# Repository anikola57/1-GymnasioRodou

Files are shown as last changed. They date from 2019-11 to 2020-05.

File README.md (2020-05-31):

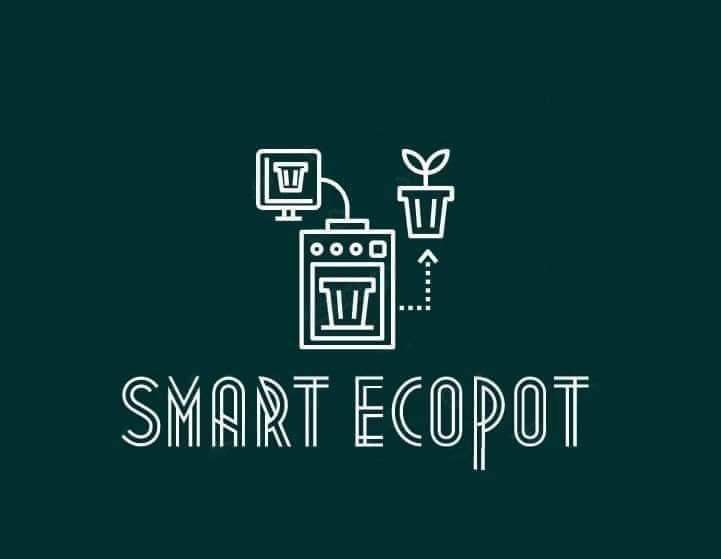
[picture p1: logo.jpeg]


---
# Smart ecoPOT
 Έξυπνο σύστημα διαχείρισης ποτίσματος

- [Περιγραφή](#Περιγραφή)
- [Θεματική](#Θεματική)
- [Τεχνολογίες - υλοποίηση](#Τεχνολογίες-υλοποίηση)
- [Ομάδα έργου](#Ομάδα)
- [Οργάνωση του έργου](#Οργάνωση)
- [Προϋπολογισμός](#Προϋπολογισμός)
- [Σύνδεσμοι](#Σύνδεσμοι)

>## Περιγραφή
Το `Smart ecoPOT` είναι μία «έξυπνη» γλάστρα στην οποία το φυτό ποτίζεται αυτόματα σύμφωνα με τις ανάγκες του. Η συγκεκριμένη λύση βασίζεται σε μετρήσεις της υγρασίας του χώματος στη γλάστρα και όταν αυτή μειωθεί κάτω από ένα όριο ενεργοποιείται μία αντλία νερού και το φυτό ποτίζεται με την απαιτούμενη ποσότητα νερού.

Το προτεινόμενο σχέδιο γλάστρας αποτελείται από τρία μικρά γλαστράκια εξάγωνου σχήματος και διαφορετικών υψών στα οποία μπορούν να φυτευτούν διάφορα φυτά. Στην κατασκευή περιλαμβάνεται η δεξαμενή νερού και ένας χώρος στον οποίο μπαίνει το ηλεκτρονικό κύκλωμα για τον έλεγχο του ποτίσματος.

Με τον έλεγχο της υγρασίας του χώματος και της παροχής νερού, τα φυτά μπορούν να αναπτυχθούν πιο υγιή. Τόσο η έλλειψη νερού όσο και το υπερβολικό πότισμα μπορούν να προκαλέσουν την καταστροφή του φυτού, ιδιαίτερα όταν πρόκειται για ευαίσθητα στην πρόσληψη νερού μυρωδικά. Με το προτεινόμενο σχέδιο το φυτό προσλαμβάνει την ποσότητα νερού που χρειάζεται για την καλύτερη ανάπτυξή του ακριβώς όταν τη χρειάζεται.

Επιπλέον, δεν απαιτείται από τον ιδιοκτήτη του φυτού να θυμάται κάθε πότε πρέπει να το ποτίσει. Το φυτό είναι αυτόνομο και απαιτείται μόνο η πλήρωση της δεξαμενής με νερό όποτε χρειάζεται. Στην περίπτωση που το νερό στη δεξαμενή εξαντλείται θα ανάβει ένα κόκκινο φωτάκι έτσι ώστε να ενημερώνεται ο ιδιοκτήτης ότι πρέπει να τη γεμίσει. Ιδιαίτερα στα απαιτητικά αστικά περιβάλλοντα αυτό είναι μία ελάφρυνση από ένα καθημερινό καθήκον.

Ένα βασικό πλεονέκτημα της κατασκευής είναι ότι γίνεται εξοικονόμηση νερού. Χρησιμοποιείται μόνο όσο νερό χρειάζεται και στο χρόνο που χρειάζεται. Αυτό είναι ιδιαίτερα σημαντικό στην εφαρμογή σε μεγαλύτερη κλίμακα.

Η γλάστρα μπορεί εύκολα να εκτυπωθεί σε 3D εκτυπωτή με βάση το σχέδιο, σε διάφορα χρώματα και μεγέθη. Είναι σχεδιασμένη έτσι ώστε να συναρμολογείται εύκολα και να χωρίζεται σε κομμάτια για να γεμίσει η δεξαμενή νερού, να πλυθεί, να ανανεωθούν τα φυτά ή ακόμα να αλλαχτούν τα εξαρτήματα της κατασκευής.

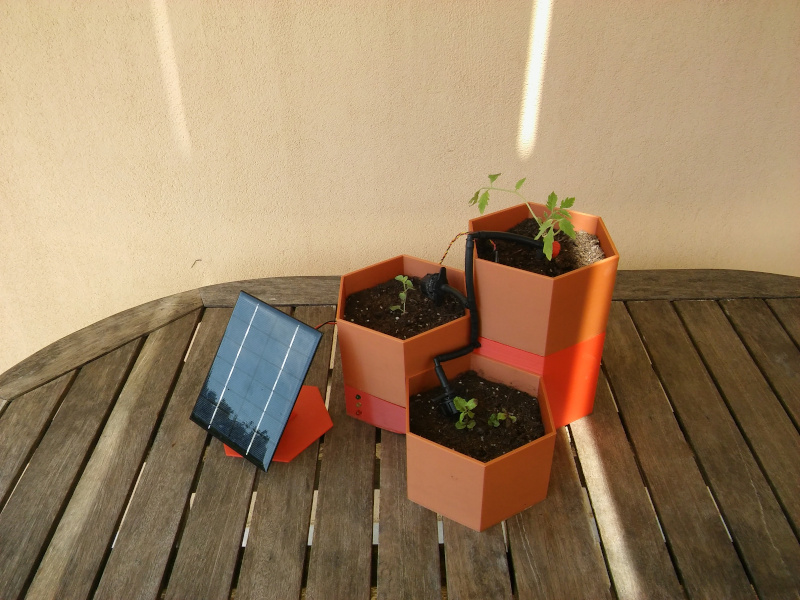
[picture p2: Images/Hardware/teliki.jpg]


Δείτε το βίντεο με την περιγραφή της κατασκευής μας.

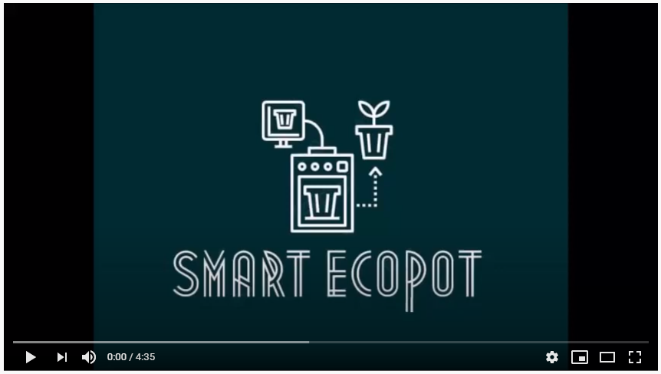
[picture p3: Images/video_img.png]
Βίντεο (https://www.youtube.com/watch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)


Και μία  [παρουσίαση](./Docs/GLASTRA.pdf) που κάναμε διαδικτυακά.

>## Θεματική
Το συγκεκριμένο έργο εντάσσεται στη θεματική της αστικής κηπουρικής, η οποία αναφέρεται στην ανάπτυξη φυτών στις πόλεις και γύρω από αυτές. Η αστική κηπουρική αποτελεί μέρος του αστικού οικοσυστήματος και της οικονομίας των πόλεων. 

Η αστική κηπουρική συμβάλει στη βελτίωση της ποιότητας της τροφής που καταναλώνεται στα αστικά κέντρα και στην προώθηση πιο υγιεινής διατροφής. Συγχρόνως, μειώνει το κόστος ενός νοικοκυριού για διατροφή αλλά και το οικολογικό αποτύπωμα της καλλιέργειας (γη, νερό, καύσιμα από τη μεταφορά της τροφής).

Η συγκεκριμένη πρόταση θα μπορούσε να επεκταθεί και για τη διαχείριση μεγαλύτερων αγροτικών εκτάσεων. Η διαχείριση του ποτίσματος μίας καλλιέργειας με αυτόν τον τρόπο θα επέφερε μεγαλύτερη εξοικονόμηση νερού και υγιείς καλλιέργειες.

>## Τεχνολογίες-υλοποίηση
Αφορμή και κίνητρο για τη συμμετοχή μας στο διαγωνισμό, είναι η αξιοποίηση του αναβαθμισμένου εξοπλισμού που παρέλαβε το σχολείο μας την περσινή χρονιά. Σε αυτόν περιλαμβάνεται ένας 3D εκτυπωτής, ένα 3D scanner, 8 εκπαιδευτικά set `Arduino Uno` και 10 σταθμοί εργασίας με `Raspberry pi`.  
Για την απόκτηση τεχνογνωσίας σχετικά με τον εξοπλισμό αυτό αξιοποιήθηκαν αποκλειστικά πηγές από το διαδίκτυο και εθελοντές ειδικοί σε σχετικούς τομείς.

Για την εκτύπωση της γλάστρας χρησιμοποιήθηκε ο 3D εκτυπωτής του Εργαστηρίου Τεχνολογίας του σχολείου. Με την αξιοποίηση του 3D εκτυπωτή κατασκευάζεται μία ολοκληρωμένη διάταξη, με τη γλάστρα, τη δεξαμενή νερού και τα ηλεκτρονικά, προσαρμοσμένη στις απαιτήσεις του έργου. 

Το αρχικό σχέδιο της γλάστρας έγινε στο online ελεύθερο λογισμικό `Tinkercad`. Στη συνέχεια λόγω μεγαλύτερης ευελιξίας προτιμήθηκε το επίσης ελεύθερο λογισμικό `Blender`. 
Αρχικό σχέδιο κατασκευής στο `Tinkercad` 

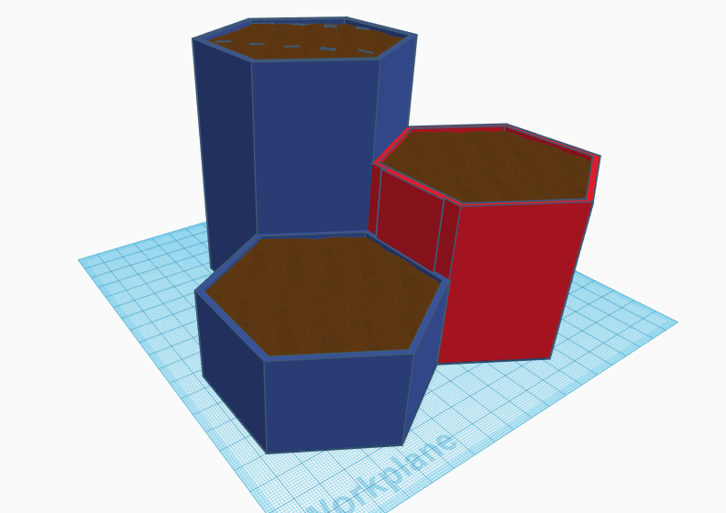
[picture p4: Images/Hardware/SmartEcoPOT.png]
 

Τελικό σχέδιο κατασκευής στο `Blender` 

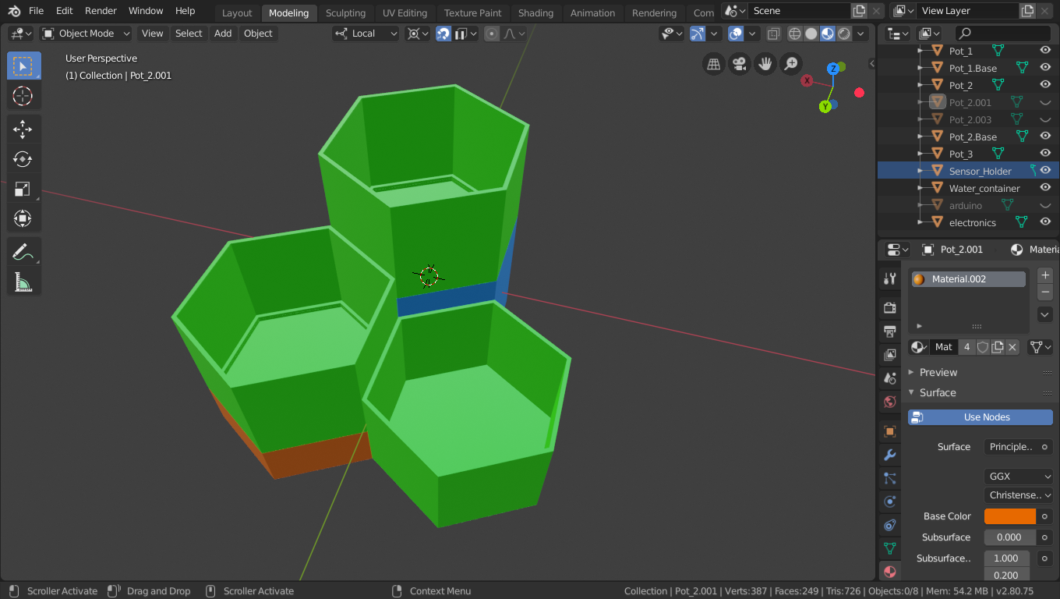
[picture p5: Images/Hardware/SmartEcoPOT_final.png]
 

Η κατασκευή αποτελείται από τρία κανονικά εξαγωνικά πρίσματα διαφορετικού ύψους, στο πάνω μέρος των οποίων έχουν προσαρτηθεί γλαστράκια ίδιου σχήματος και ύψους με το μικρότερο από τα πρίσματα. Τα γλαστράκια είναι αποσπώμενα έτσι ώστε να μπορούν να γεμίσουν με χώμα και να φυτευτούν. Το κάτω μέρος από το μεγαλύτερο από τα εξάγωνα είναι η δεξαμενή νερού και στο αντίστοιχο κάτω μέρος από το μεσαίο γλαστράκι μπαίνει το κύκλωμα με το Arduino. 

Για τον έλεγχο της στάθμης του νερού και της υγρασίας του χώματος χρησιμοποιείται `Arduino Uno`. Για τη μέτρηση της υγρασίας του χώματος χρησιμοποιείται αναλογικός αισθητήρας υγρασίας ο οποίος δίνει μία τιμή στο πρόγραμμα ανάλογα με την υγρασία του χώματος. Το πρόγραμμα μετατρέπει αυτή την τιμή σε ποσοστό %. Για τη μέτρηση της στάθμης νερού τοποθετηθηκε στη δεξαμενή ένας δεύτερος αισθητήρας υγρασίας που δίνει σήμα ανάλογα με τη στάθμη του νερού. Υπάρχει ακόμα μία αντλία ποτίσματος, η οποία συνδέεται μέσω κατάλληλης διάταξης για την ενίσχυση του ρεύματος, σε μία ψηφιακή έξοδο του Arduino. Το οριστικό σχηματικό διάγραμμα του κυκλώματος έγινε στο fritzing και είναι το παρακάτω:

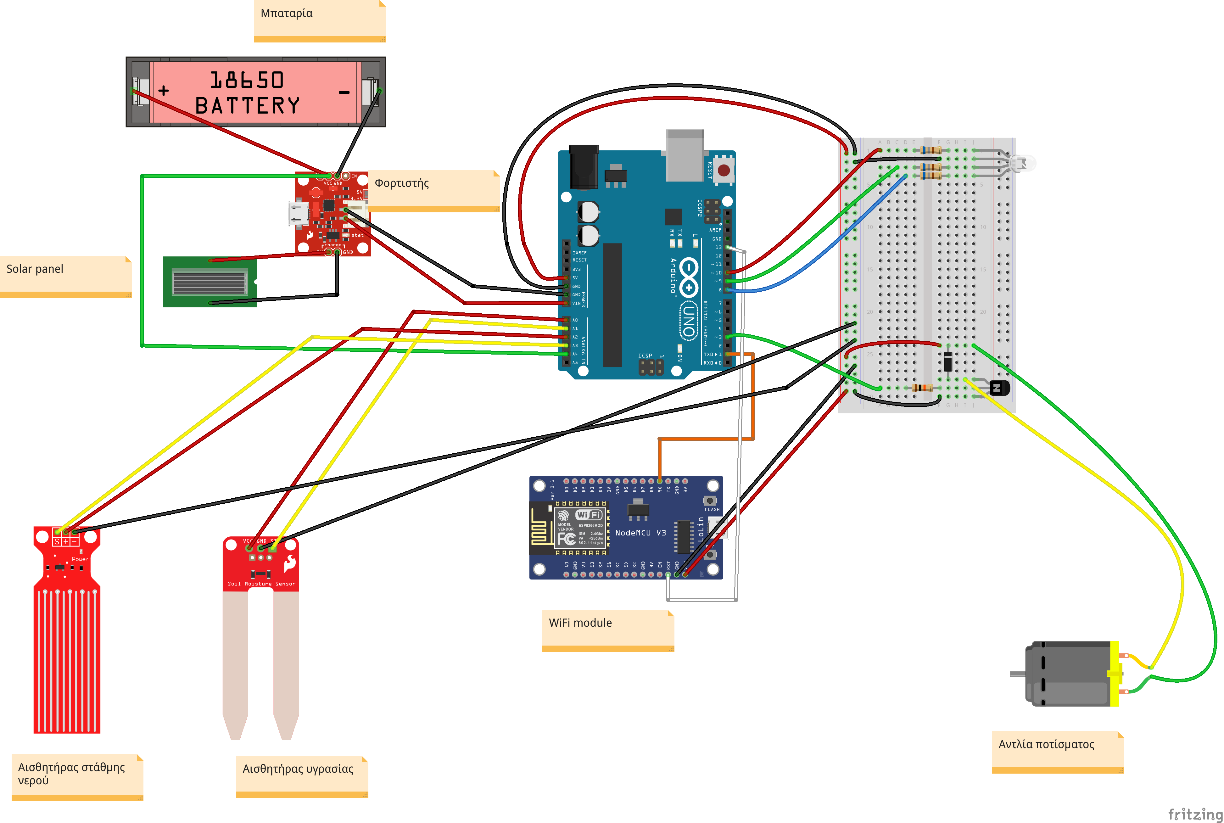
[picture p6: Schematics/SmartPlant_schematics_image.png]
 

Για την προβολή της κατάστασης του συστήματος υπάρχουν ενδεικτικά led τα οποία ειδοποιούν για την κατάσταση της υγρασίας του χώματος, την επάρκεια νερού στη δεξαμενή και την κατάσταση ποτίσματος. Το κύκλωμα τροφοδοτείται είτε από τροφοδοτικό είτε εναλλακτικά από επαναφορτιζόμενη μπαταρία με φωτοβολταϊκό πάνελ. Για τη στήριξη του φωτοβολταϊκού σχεδιάστηκε και τυπώθηκε στον 3D εκτυπωτή μία βάση.

Το λογισμικό για τον έλεγχο των αισθητήρων, της αντλίας και των ενδείξεων αναπτύχθηκε στην πλατφόρμα Arduino. Ένα βασικό διάγραμμα ροής του προγράμματος υπάρχει στον φάκελο [Docs](./Docs/flowchart_1.pdf)

Για την αναπαραγωγή του έργου δίνεται το σχέδιο της [γλάστρας](./3D/) για εκτύπωση σε 3D εκτυπωτή, το σχέδιο του [κυκλώματος](./Schematics/) και το [πρόγραμμα](./Source/)  .

Στην κατασκευή ενσωματώθηκε ένα WiFi module για τη βελτίωση της εποπτείας της κατάστασης. Μέσω αυτού στέλνονται τα δεδομένα της γλάστρας, όπως υγρασία χώματος και στάθμη νερού, στην πλατφόρμα ThingSpeak. Από εκεί υπάρχει η δυνατότητα παρακολούθησης της κατάστασης σε πραγματικό χρόνο μέσω μίας ιστοσελίδας.

>## Ομάδα
Στο έργο συμμετείχαν μαθητές της Β' τάξης του 1ου Γυμνασίου Ρόδου υπό την καθοδήγηση της καθηγήτριας τεχνολογίας Αγγελικής Νικολάου.
Οι συναντήσεις των μαθητών γινόντουσαν μετά το σχολικό ωράριο στο χώρο του σχολείου. Μετά το κλείσιμο των σχολείων λόγω κοροναϊού, οι συναντήσεις συνεχίστηκαν με το https://jitsi.org/jitsi-meet/.  Αν και όλοι οι μαθητές συνεργάστηκαν μεταξύ τους για το έργο, δημιουργήθηκαν κάποιες ομάδες οι οποίες ανέλαβαν ένα μέρος του. Συγκεκριμένα οι ομάδες είναι οι ακόλουθες:

    Προγραμματιστές
    Ασχολήθηκαν κυρίως με την ανάπτυξη του λογισμικού για το Arduino.
---
    Σχεδιαστές
    Σχεδίασαν τη γλάστρα για την εκτύπωση στον 3D εκτυπωτή. 
---
    Ηλεκτρονικοί
    Σχεδίασαν το κύκλωμα και συντόνισαν την υλοποίηση της κατασκευής.  

Φωτογραφίες της ομάδας επί το έργον, υπάρχουν στον φάκελο [Images/Act](./Images/Act).

> ## Οργάνωση
Ο τρόπος οργάνωσης και υλοποίησης καθώς και το πλαίσιο του έργου περιγράφεται αναλυτικά στο σχετικό [αρχείο](./Docs/ConceptOfProject.pdf).

> ## Προϋπολογισμός
Κόστος έργου για τη βασική κατασκευή:

Ειδος|Τιμή
---|---:
Arduino Nano OEM|4,50€
Βυθιζόμενη αντλία|5€
Σωληνάκι|0,60€
Transistor|0,05€
Αντιστάσεις|0,05€
Καλώδια|1€
LED|0,20€
Αισθητήρας στάθμης νερού|2€
Αισθητήρες υγρασίας εδάφους|2€
Breadboard|1€
PLA|6€
ΣΥΝΟΛΟ|22,40€

Κόστος έργου με επιλογή για τροφοδοτικό:

Ειδος|Τιμή
---|---:
Βασική κατασκευή|22,40€
Τροφοδοτικό|5€
ΣΥΝΟΛΟ|27,40€

Κόστος έργου με επιλογή για φωτοβολταϊκό και επαναφορτιζόμενη μπαταρία:

Ειδος|Τιμή
---|---:
Βασική κατασκευή|22,40€
Φωτοβολταϊκό πάνελ 5v, 1w|3€
Επαναφορτιζόμενη μπαταρία 18650 3400mAh|4,40€
Κύκλωμα φόρτισης φωτοβολταϊκού CN3065|3,80€
Κύκλωμα φόρτισης μπαταρίας 134N3P|1,20€
ΣΥΝΟΛΟ|34,80€

Το κόστος για την επέκταση της κατασκευής με το wifi module:

Ειδος|Τιμή
---|---:
NodeMCU|7€

> ## Σύνδεσμοι

2ος Πανελλήνιος Διαγωνισμός Ανοιχτών Τεχνολογιών στην Εκπαίδευση https://robotics.ellak.gr/

Arduino https://www.arduino.cc

3D printer Ultimaker 2+ https://ultimaker.com/3d-printers/ultimaker-2-plus 

Tinkercad https://www.tinkercad.com/

fritzing https://fritzing.org/

ThingSpeak https://thingspeak.com/

Blender https://www.blender.org/

Αστική κηπουρική https://www.ruaf.org/urban-agriculture-what-and-why

1ο Γυμνάσιο Ρόδου http://1gym-rodou.dod.sch.gr/wp/

---

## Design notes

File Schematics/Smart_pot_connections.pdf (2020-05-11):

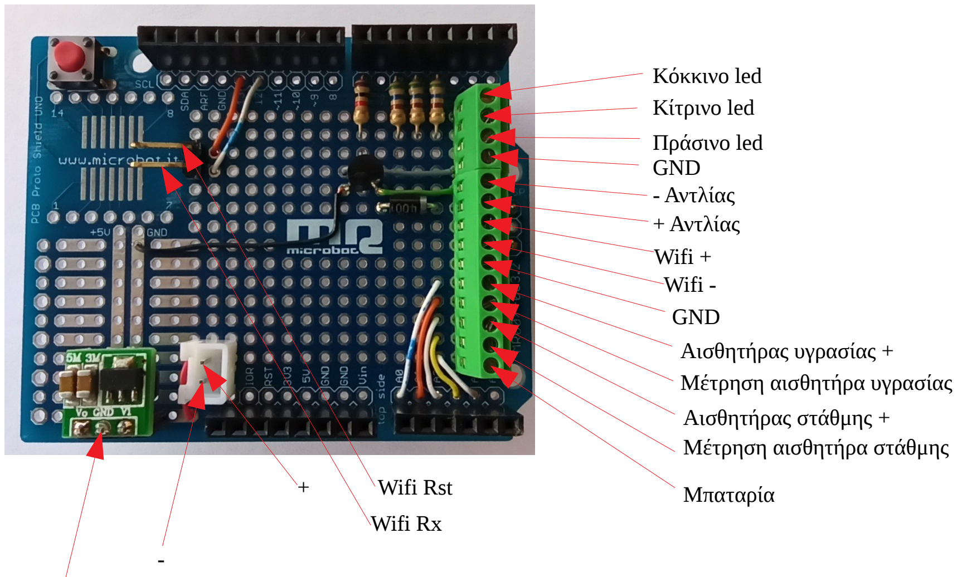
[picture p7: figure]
Κόκκινο ledled Κίτρινο ledled Πράσινο ledled GND - ledΑντλίας + ledΑντλίας Wifi led+ Wifi led- GND Αισθητήρας ledυγρασίας led+ Μέτρηση ledαισθητήρα ledυγρασίας Αισθητήρας ledστάθμης led+ Μέτρηση ledαισθητήρα ledστάθμης; Μπαταρία +; Wifi ledRx; Wifi ledRst

Μετατροπέας led4.2v σε 5vv ledσε led5vv

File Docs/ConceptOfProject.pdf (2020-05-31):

# SMART ECOPOT

1

# Ο ΓΥΜΝΑΣΙΟ ΡΟΔΟΥ

### Υπεύθυνη εκπαιδευτικός: Αγγελική Νικολάου, Αρχιτέκτων

# ΤΟ CONCEPT ΤΟΥ ΕΡΓΟΥ ΜΑΣ

Το Μάρτιο του 2019 το σχολείο παρέλαβε αναβαθμισμένο τεχνολογικό εξοπλισμό για τον οποίο δεν υπήρχε πρόβλεψη που θα τοποθετηθεί και από ποιους εκπαιδευτικούς θα αξιοποιηθεί. Επιπλέον επειδή δεν υπήρξε καμία επιμόρφωση, το υλικό αυτό παρέμενε αχρησιμοποίητο.

Με αφορμή την επιθυμία ομάδας παιδιών της Β΄ Γυμνασίου να χρησιμοποιήσουμε τον τρισδιάστατο εκτυπωτή, αναλάβαμε τη δημιουργία ενός έργου, πέρα από τα πλαίσια κάποιου μαθήματος. Ενός πρότζεκτ που θα εντασσόταν σε ένα πλαίσιο συνεργασιών και θα είχε σκοπό που θα υπερέβαινε όλους μαζί και τον καθένα ξεχωριστά, μαθητές και εκπαιδευτικό.

Θεωρούμε ότι η εμπειρία αυτού του τύπου έργων για την εποχή μας, την εποχή των ραγδαίων αλλαγών, είναι πολύ σημαντική για ένα παιδί Γυμνασίου, το οποίο έχει την αναπτυξιακή ωριμότητα να καταλάβει τη διαδικασία, να τη διεκπεραιώσει και να τη δέσει με την εργασία των άλλων-συνεργατών.

Όσον αφορά τη θέση μας στον παιδαγωγικό χάρτη, γνωρίζουμε ότι η επιστήμη τείνει προς την κατεύθυνση της ανάλυσης αλλά και ότι στη σύγχρονη πραγματικότητα η γνώση είναι σωρευτική. Στην τεχνολογία γενικότερα κάνουμε πράγματα, κινούμενοι προς την κατεύθυνση του σχεδιασμού και της κατασκευής. Στόχος μας είναι τα παιδιά να συνεργαστούν και να αξιοποιήσουν τη γνώση των άλλων, προσπαθώντας να λύσουν ένα πρόβλημα. Εν προκειμένω η ανάλυση καταλαμβάνει μικρότερο μέρος και μεγαλύτερη έμφαση δίνεται στο σχεδιασμό της λύσης του προβλήματος και τη σύνθεση.

Ανατρέχοντας στο διαδίκτυο είναι γνωστό ότι μπορούμε να εντοπίσουμε, να αξιοποιήσουμε και να ωφεληθούμε από τη γνώση άλλων, οι οποίοι πριν από εμάς «ανακάλυψαν τον τροχό». Δεν αγνοούμε αυτού του τύπου τη γνώση, αλλά αντιθέτως προσπαθούμε να την αξιοποιήσουμε προς όφελος όλων. Το παιδί παρακολουθώντας αυτή τη διαδικασία και συμμετέχοντας στην αναζήτηση, αποκτά μια πολύ σημαντική και ωφέλιμη εμπειρία: ότι αξιοποιώντας τη γνώση των άλλων για να λύσουμε ένα πραγματικό πρόβλημα, ίσως οδηγηθούμε προς την καινοτομία. Με αυτό τον τρόπο, μπορούμε να του θέσουμε ερωτήματα, που θα του δημιουργήσουν την επιθυμία να ανελιχθεί σε πιο σύνθετα ερωτήματα και που ίσως το οδηγήσουν σε νέα γνώση αργότερα.

Η παρουσίαση μας αυτή, μεταξύ άλλων έχει σκοπό να καταθέσει την εμπειρία που αποκτήθηκε από τη σκοπιά που περιγράψαμε παραπάνω, ώστε στο μέλλον να υπάρξουν περισσότεροι εκπαιδευτικοί, από διαφορετικές ειδικότητες που θα εμπλακούν, με στόχο τη δημιουργική επίλυση προβλημάτων και την αξιοποίηση πόρων της παγκόσμιας κοινότητας που διακινεί και διαμοιράζεται ανοιχτό υλικό.

# ΟΡΓΑΝΩΣΗ ΤΟΥ PROJECT

### Σεπτέμβριος 2019

Έναρξη του πρότζεκτ, με την ανακοίνωση του διαγωνισμού ο οποίος αποτέλεσε μια καλή ευκαιρία εμπλοκής μαθητών στην αξιοποίηση του αναβαθμισμένου ψηφιακού εξοπλισμού που διέθετε το 1ο Γυμνάσιο Ρόδου, τον Μάρτιο του 2019.

Η ομάδα συγκροτήθηκε άμεσα (12 μαθητές Α΄ και Β΄ Γυμνασίου) και οι συναντήσεις ορίστηκαν κάθε Τρίτη μια ώρα, μετά το σχόλασμα και τις Κυριακές για περισσότερο χρόνο. Με ιδεοθύελλα και αναζήτηση στο ίντερνετ αλλά και από το περιβάλλον των γνωστών των παιδιών, καταλήξαμε στον τομέα της αστικής κηπουρικής και της γεωργίας ακριβείας. Αποφασίσαμε να δημιουργήσουμε ένα αυτόνομο σύστημα από γλάστρες, οι οποίες θα λύνουν το πρόβλημα της καλλιέργειας σε αστικό προβάλλον, (βεράντα, ταράτσα, κήπο, αγρόκτημα). Με δυνατότητα ποτίσματος όταν το έχει ανάγκη το φυτό και αισθητήρες για να ειδοποιούν τον κάτοχο για τα στοιχεία που τον ενδιαφέρουν, όπως, υγρασία εδάφους, στάθμη νερού και άλλα χαρακτηριστικά.

Επειδή το πρότζεκτ ξεπερνούσε τις δυνατότητες όλων μας, παιδιών και εκπαιδευτικού, και επειδή η γνώση υπάρχει «εκεί έξω», δύο ήταν οι επόμενες κινήσεις. Πρώτον, να δούμε τι έχουν κάνει άλλοι πριν από εμάς και δεύτερον ποιους θα εμπλέξουμε εθελοντικά κυρίως στο κομμάτι του κώδικα και των ηλεκτρονικών.

Βήμα 1

ο

Αναζήτηση στο διαδίκτυο για πρότζεκτ που έχουν υλοποιηθεί με arduino.

https://www.instructables.com/circuits/arduino/projects/

https://www.instructables.com/circuits/projects/

https://www.instructables.com/id/9-12-Projects-High-School/

https://create.arduino.cc/projecthub/projects/tags/kids

https://www.makerspaces.com/15-simple-arduino-uno-breadboard-projects/

https://www.circuito.io/blog/arduino-projects-for-beginners/

https://www.youtube.com/watch?v=PfvqunpN7M4

Εκπαιδευτικό Υλικό για Arduino Uno

Προγραμματίζοντας με τον μικροελεγκτή Arduino

http://users.sch.gr/manpoul/docs/arduino/ProgrammingArduino.pdf

http://3gym-igoum.thesp.sch.gr/images/Arduino/book.pdf

https://www.vodafonegenerationnext.gr/learn/arduino-basics

http://robotics-edu.gr/data/arduino/arduino_paliouras.pdfhttps://www.youtube.com/watch?v=62MGqPIyoDg

https://www.youtube.com/watch?v=SlU7ADUIgtI

Βήμα 2

ο
: Αναζήτηση συνεργατών με γνώσεις χρήσης Arduino και ηλεκτρονικών

Αξιοποιώντας το προσωπικό μαθησιακό δίκτυο (PLN), έγιναν οι παρακάτω δράσεις:

- Στην πρώτη συγκέντρωση ενημέρωσης γονέων μετά τον αγιασμό του σχολείου, ανακοινώθηκε η πρόσκληση εθελοντικής συμμετοχής γονέων-συνεργατών για την αξιοποίηση του ψηφιακού εξοπλισμού του σχολείου.
- Στάλθηκαν emails με πρόσκληση προς όλους τους εκπαιδευτικούς της Ρόδου, από τις διευθύνσεις Πρωτοβάθμιας και Δευτεροβάθμιας Εκπαίδευσης Δωδεκανήσου, για εθελοντική συμμετοχή σε καινοτόμο πρόγραμμα.
- Στάλθηκαν emails από τη γραμματεία της Σχολής Ανθρωπιστικών σπουδών του Παν/μίου Αιγαίου προς όλους, διδακτικό προσωπικό και φοιτητές.
- ‘Έγινε αναζήτηση εθελοντών μέσω του Tipping point https://www.thetippingpoint.org.gr/ και 100 mentors https://platform.100mentors.com/community/tippingpoint

Το αποτέλεσμα ήταν να βρεθούν εθελοντές: οι γονείς μαθητή μας, οι κ. & κ. Γρίβας (μαθηματικός και ηλεκτρονικός), ο διδάσκων από το Παν/μιο Αιγαίου κ. Ν. Ταψής (φυσικός) και ο μέντορας από το tipping point κ. Η. Ψυρούκης (ηλεκτρολόγος μηχ/κος).

### Οκτώβριος- Νοέμβριος- Δεκέμβριος 2019

Διατύπωση του προβλήματος και η λύση

Διατυπώθηκε το πρόβλημα που αντιμετωπίζουν οι πολυάσχολοι κάτοικοι της πόλης, όταν καλλιεργούν φυτά σε βεράντες, ταράτσες ή κήπους.

Πρόβλημα: Έλλειψη νερού στο φυτό ή σπατάλη νερού, όταν χρησιμοποιούνται τα γνωστά συστήματα αυτόματου ποτίσματος, που κυκλοφορούν στην αγορά.

Λύση: Σωστή ποσότητα νερού που χρειάζεται το φυτό, την ώρα που το χρειάζεται με προγραμματισμό ποτίσματος, από αισθητήρα υγρασίας χώματος. Η αντλία νερού που θα βυθίζεται σε δεξαμενή ενσωματωμένη στη γλάστρα, θα περιέχει αισθητήρα στάθμης νερού για να δίνει φωτεινό σήμα (θα ανάβει led) όταν το νερό κατεβαίνει κάτω από ένα επίπεδο. Η επαναφορτιζόμενη πηγή θα φορτίζεται από ηλιακό πάνελ.

Εξοπλισμός και αναζήτηση στο διαδίκτυο υλικών-ηλεκτρονικών κατασκευής

Γλάστρα, αισθητήρας υγρασίας χώματος, δεξαμενή νερού, αισθητήρας στάθμης νερού, αντλία νερού, σωληνάκια ποτίσματος, λεντάκια με ενδείξεις για τη στάθμη του νερού στη δεξαμενή, μικροελεγκτής Arduino Uno, ηλιακό πάνελ για τη φόρτιση της μπαταρίας και ασύρματη επικοινωνία των δεδομένων των αισθητήρων.

Διάγραμμα ροής

Τα παιδιά δημιούργησαν στον πίνακα του σχολείου το διάγραμμα ροής.

Εξοικείωση με τον προγραμματισμό

Η ομάδα μέσω της πλατφόρμας του The tipping point, άρχισε μαθήματα εξοικείωσης με τον προγραμματισμό για Arduino. Οι μαθητές ανταποκρίθηκαν με ενθουσιασμό στην από απόσταση
διδασκαλία. | Από | το | διαδικτυακό | υλικό
http://users.sch.gr/manpoul/docs/arduino/ProgrammingArduino.pdf | επιλεκτικά | οι | μαθητές
εξερεύνησαν τις βασικές αρχές στον προγραμματισμό του Arduino και στα κυκλώματα.

Στη συνέχεια με κατάλληλη καθοδήγηση τα παιδιά αναζήτησαν στο διαδίκτυο δημοσιευμένα προγράμματα που αφορούσαν αυτόνομο πότισμα, αισθητήρες υγρασίας, λειτουργία αντλίας και LED.

Επέλεξαν | το | πρόγραμμα | που | ικανοποιούσε | τις | βασικές | αρχές | της | λύσης | τους
https://www.youtube.com/watch?v=T_tpKoNCVYw και χρησιμοποίησαν ως βάση αυτόν τον κώδικα, για να τον επεκτείνουν ώστε να ικανοποιεί τις ανάγκες του δικού τους πρότζεκτ.

Στις επόμενες συναντήσεις χωρίσαμε τον κώδικα σε τμήματα και πειραματιστήκαμε με κομμάτια του κώδικα που αφορούσαν στα παρακάτω:

1. Λειτουργία LED
2. Λειτουργία αισθητήρα υγρασίας χώματος
3. Λειτουργία αντλίας στη δεξαμενή νερού
4. Λειτουργία στάθμης νερού στη δεξαμενή

### Ιανουάριος 2020

ΣΧΕΔΙΑΣΜΟΣ ΤΡΙΣΔΙΑΣΤΑΤΟΥ ΜΟΝΤΕΛΟΥ ΤΗΣ ΓΛΑΣΤΡΑΣ

Αρχικά ο σχεδιασμός της γλάστρας έγινε στο χαρτί. Στη συνέχεια δημιουργήθηκε μακέτα του συστήματος των γλαστρών με μακετόχαρτο, για να δοκιμαστούν τα ηλεκτρονικά και να ελεγχτούν οι διαστάσεις, πριν τη σχεδίαση στον υπολογιστή.

Στη συνέχεια τα παιδιά άρχισαν να σχεδιάζουν τη γλάστρα με το πρόγραμμα Tinkercad, το οποίο είναι online και πολύ φιλικό για τα παιδιά γυμνασίου, αφού πρώτα αναζήτησαν στο διαδίκτυο tutorials. Να σημειωθεί ότι το ίδιο το Tinkercad παρέχει βίντεο με οδηγίες.

Με το Tinkercad έγινε η αρχική σχεδίαση της γλάστρας, αν και κάποια παιδιά είχαν βασικές γνώσεις Sketchup. Τελικά ένα μαθητής έμαθε το σχεδιαστικό πρόγραμμα Blender https://www.blender.org/, στο οποίο έγινε και το τελικό, βελτιωμένο σχέδιο του συστήματος των γλαστρών.

Τα τμήματα του συστήματος εκτυπώθηκαν με PLA, βιοδιασπώμενο υλικό, από τον εκτυπωτή του σχολείου, αφού πρώτα έγιναν οι κατάλληλες παραμετροποιήσεις με το πρόγραμμα CURA. Οι δοκιμές και οι αποτυχίες στην τρισδιάστατη εκτύπωση, ήταν ο τρόπος που οδήγησε στο τελικό αποδεκτό αποτέλεσμα.

### Φεβρουάριος 2020

Ολοκληρώθηκε το πρόγραμμα που δημοσιεύθηκε στο Github https://github.com/anikola57/1-GymnasioRodou (https://github.com/anikola57/1-GymnasioRodou) καθώς κα η εκτύπωση της γλάστρας.

Οι πρώτες δοκιμές των ηλεκτρονικών στην εκτυπωμένη γλάστρα έγιναν στο σχολείο.

### Μάρτιος 2020

Καθώς η ολοκλήρωση του έργου φαινόταν ότι πλησίαζε, η ομάδα σκέφτηκε να κάνει κάποιες βελτιώσεις και επεκτάσεις στο σύστημα των γλαστρών. Επικράτησε η πρόταση το σύστημα να είναι ενεργειακά αυτόνομο και να ελέγχεται από απόσταση.

Σε αυτή τη φάση σταμάτησαν οι δια ζώσης συναντήσεις στο σχολείο λόγω κορονοϊού.

Οι συναντήσεις πλέον γινόντουσαν με το https://jitsi.org/jitsi-meet/. Η γλάστρα μεταφέρθηκε στο σπίτι μαθητή της ομάδας. Με τη βοήθεια του γονέα, προστέθηκε το ηλιακό πάνελ και η ασύρματη επικοινωνία του συστήματος με ιστοσελίδα για τον έλεγχο των δεδομένων από απόσταση (https://thingspeak.com/channels/1026147).

Η οργάνωση της παρουσίασης έγινε και αυτή από απόσταση. Οι μαθητές συνεργάστηκαν και βιντεοσκόπησαν, με αρκετή δυσκολία, τον εαυτό τους για να δημιουργηθεί το τελικό βίντεο της παρουσίασης, το οποίο είναι στο https://www.youtube.com/watch?v=l_-LzqQXOXw.

Φωτογραφίες εν ώρα δράσης

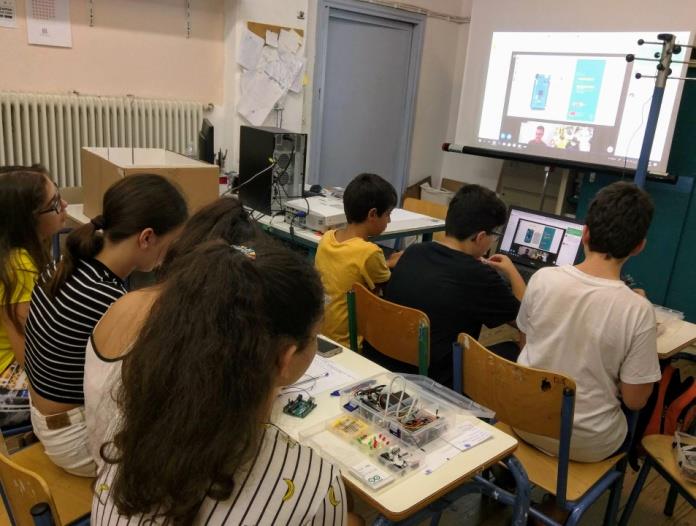
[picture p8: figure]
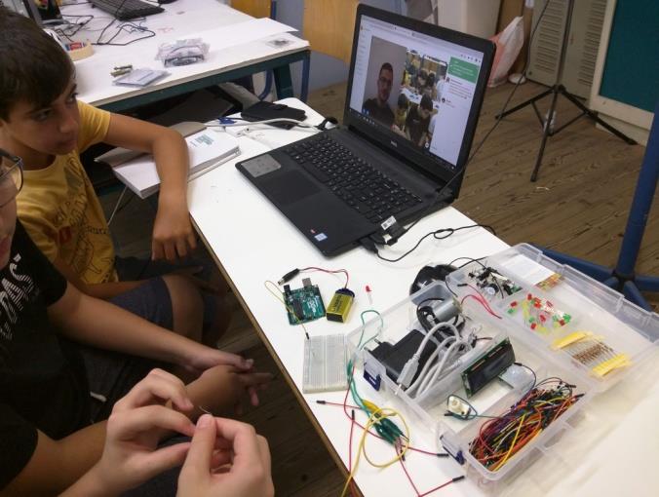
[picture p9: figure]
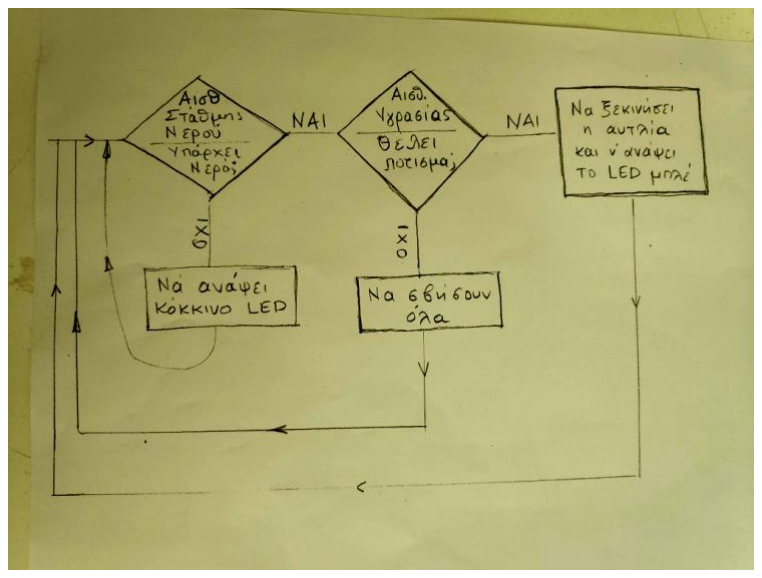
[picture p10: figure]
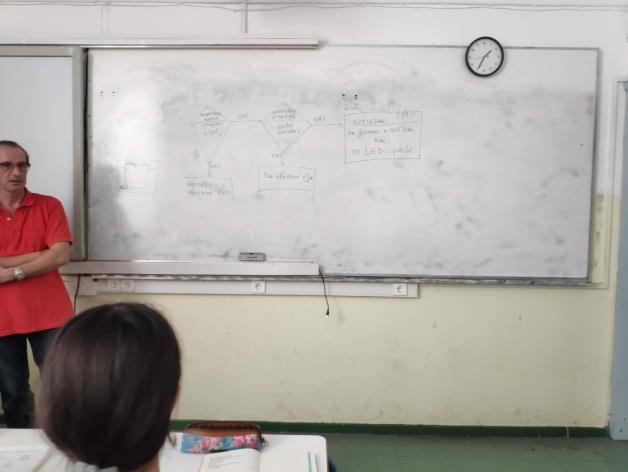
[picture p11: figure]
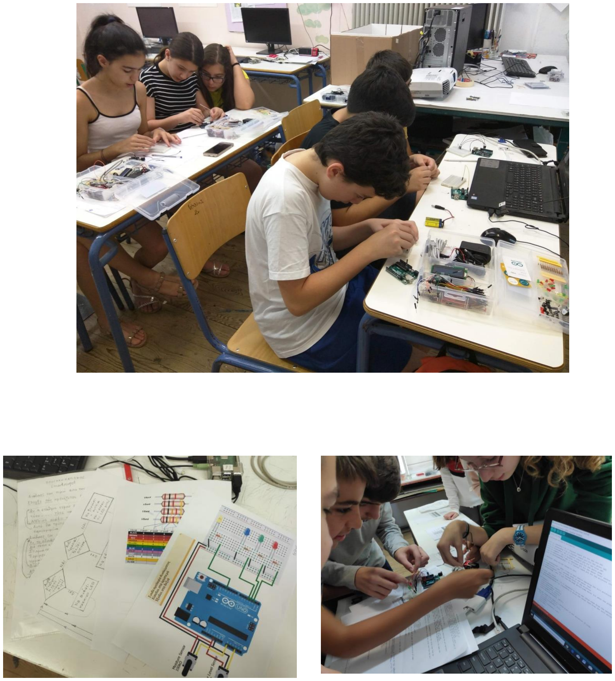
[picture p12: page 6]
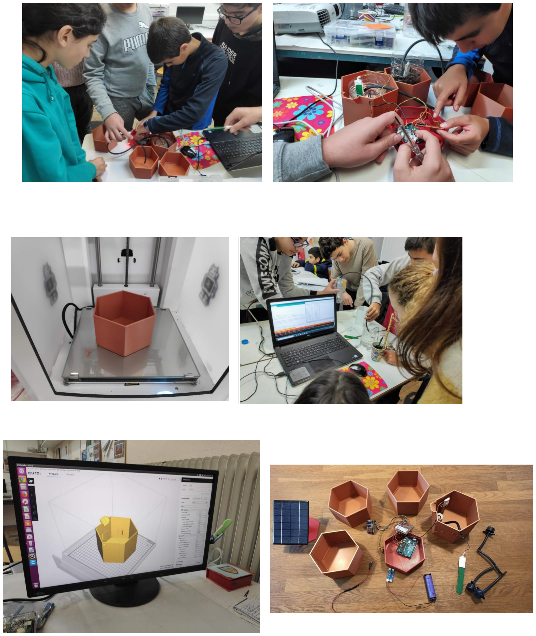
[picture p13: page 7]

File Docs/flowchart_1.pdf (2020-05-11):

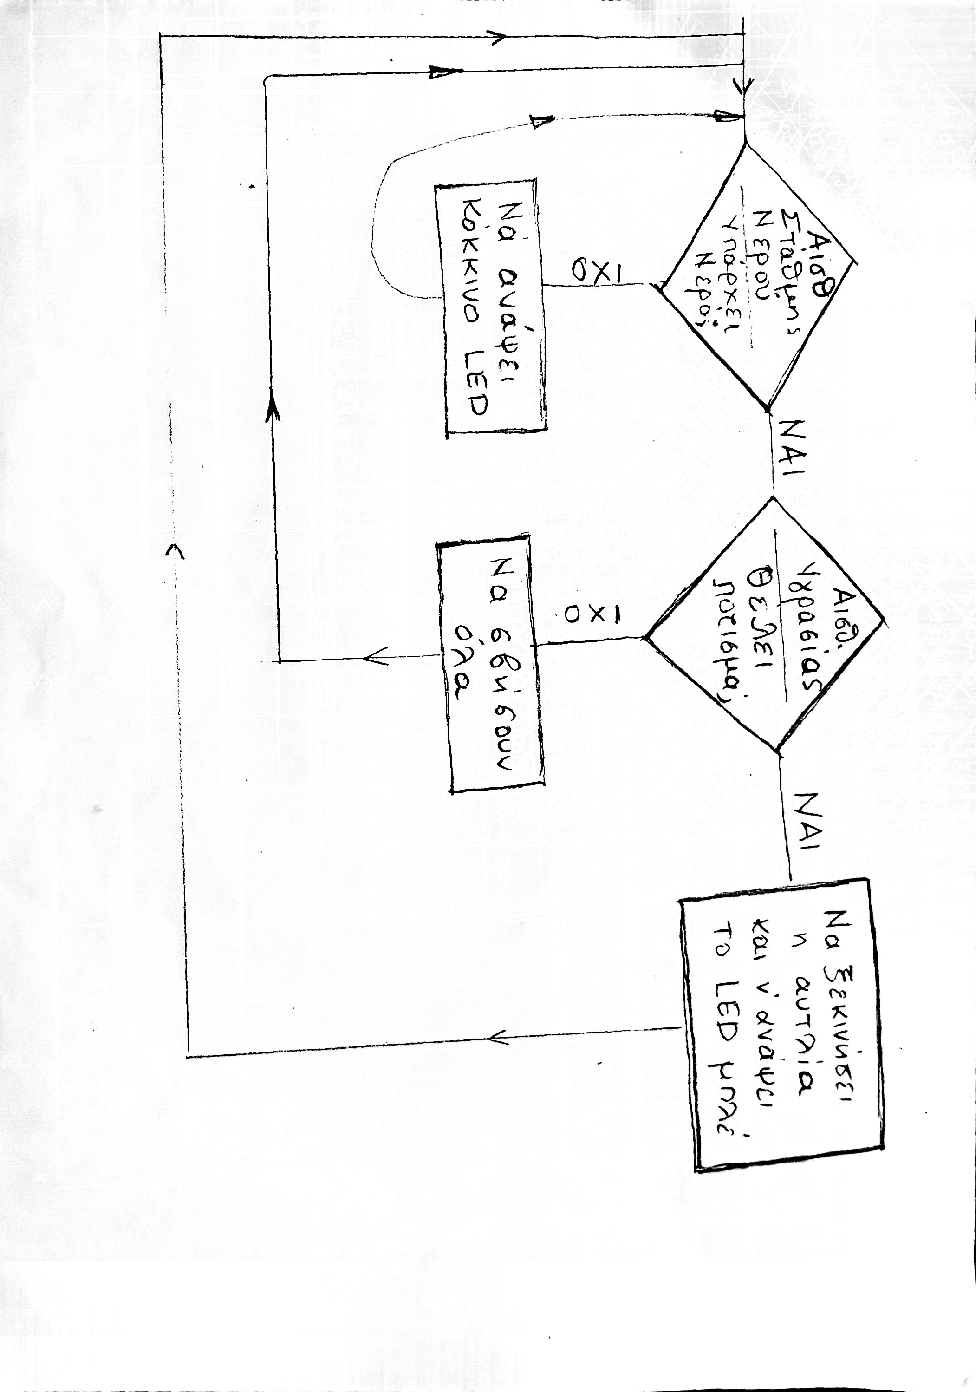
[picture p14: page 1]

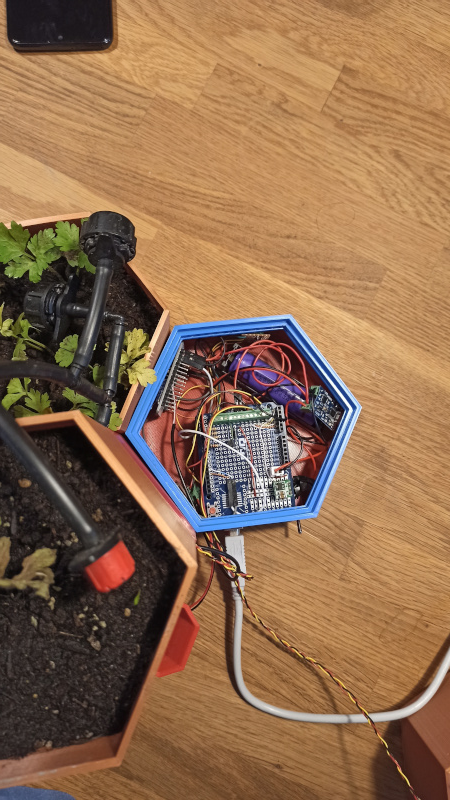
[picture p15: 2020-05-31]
Images/Hardware/electronics.jpg

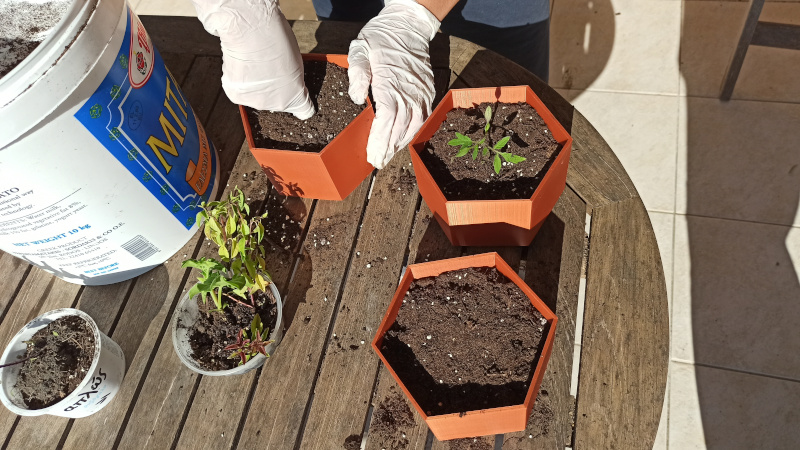
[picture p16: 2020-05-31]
Images/Hardware/planting.jpg

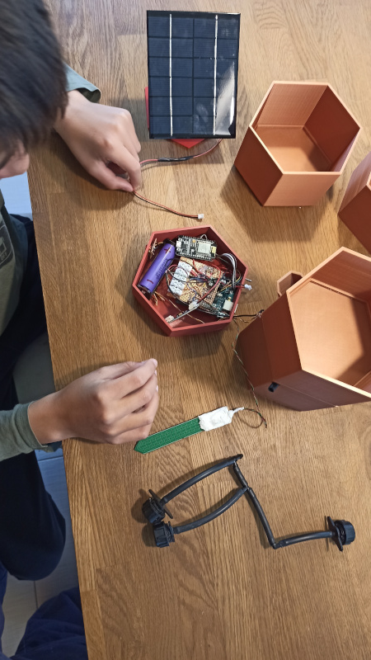
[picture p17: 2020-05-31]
Images/Hardware/sinarmologisi.jpg

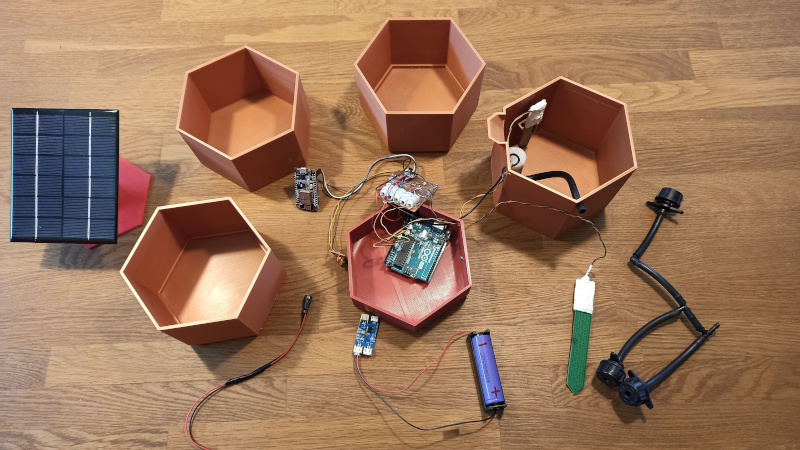
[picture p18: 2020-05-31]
Images/Hardware/kataskevi.jpg

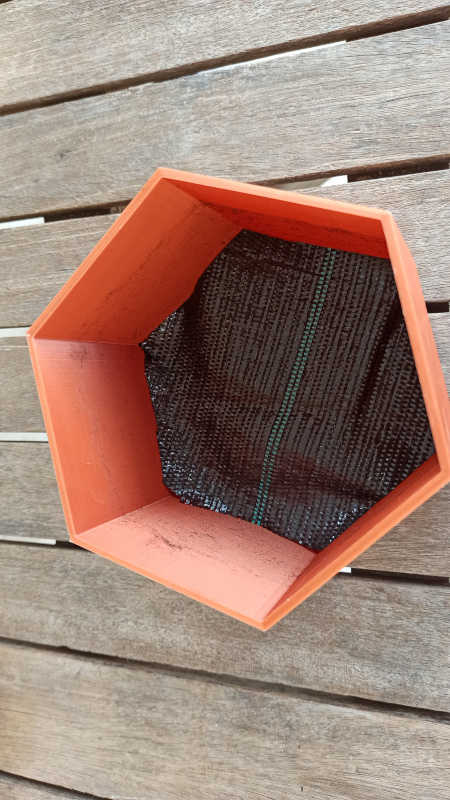
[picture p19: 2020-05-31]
Images/Hardware/interior.jpg

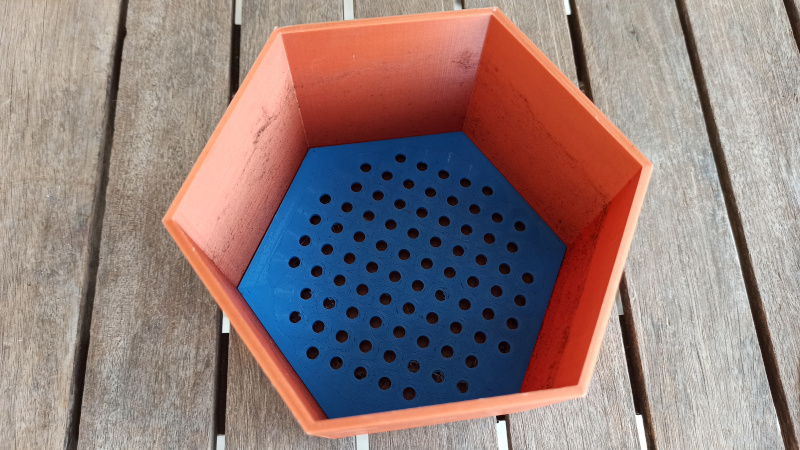
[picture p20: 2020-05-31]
Images/Hardware/basi.jpg

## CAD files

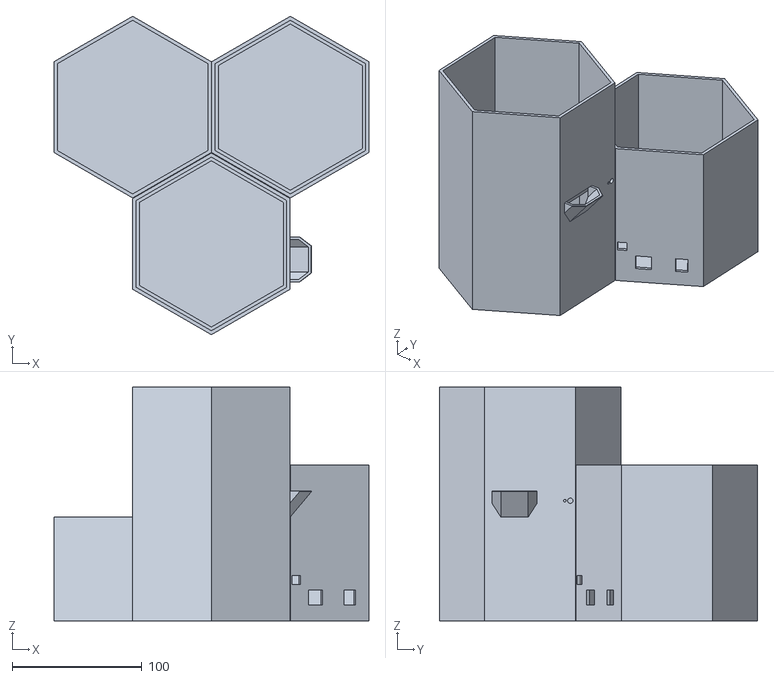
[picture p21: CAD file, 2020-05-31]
3D/stl_files/smartPot.stl
242.7 x 245.4 x 180.0

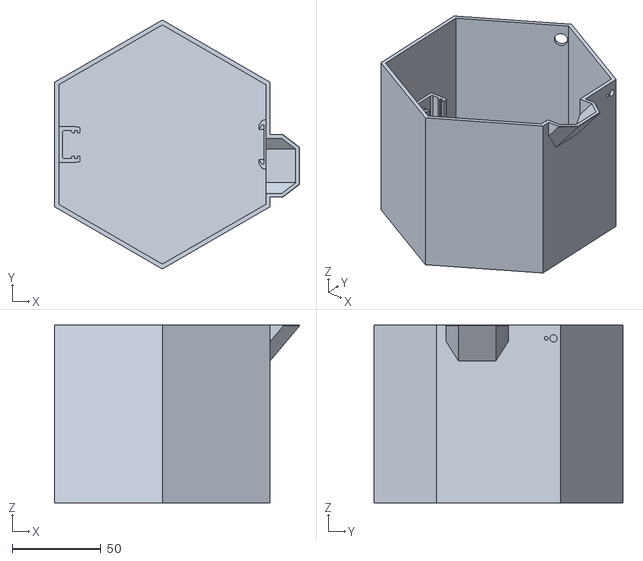
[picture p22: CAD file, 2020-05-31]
3D/stl_files/smartPot_water_container.stl
137.8 x 140.0 x 100.0

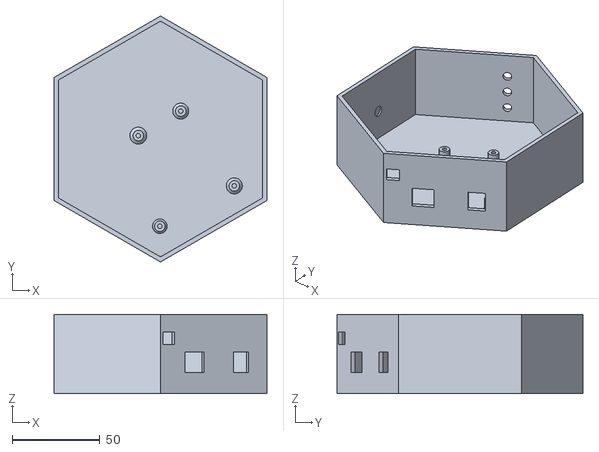
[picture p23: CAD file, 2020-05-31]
3D/stl_files/smartPot_electronics.stl
121.2 x 140.0 x 45.0

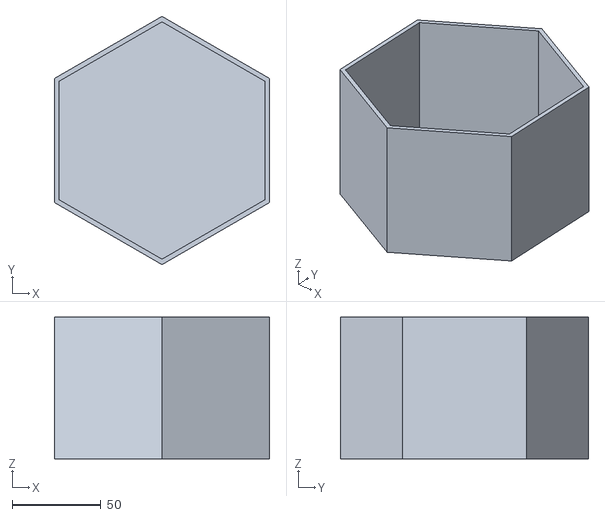
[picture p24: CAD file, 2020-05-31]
3D/stl_files/smartPot_pot1.stl
121.2 x 140.0 x 80.0

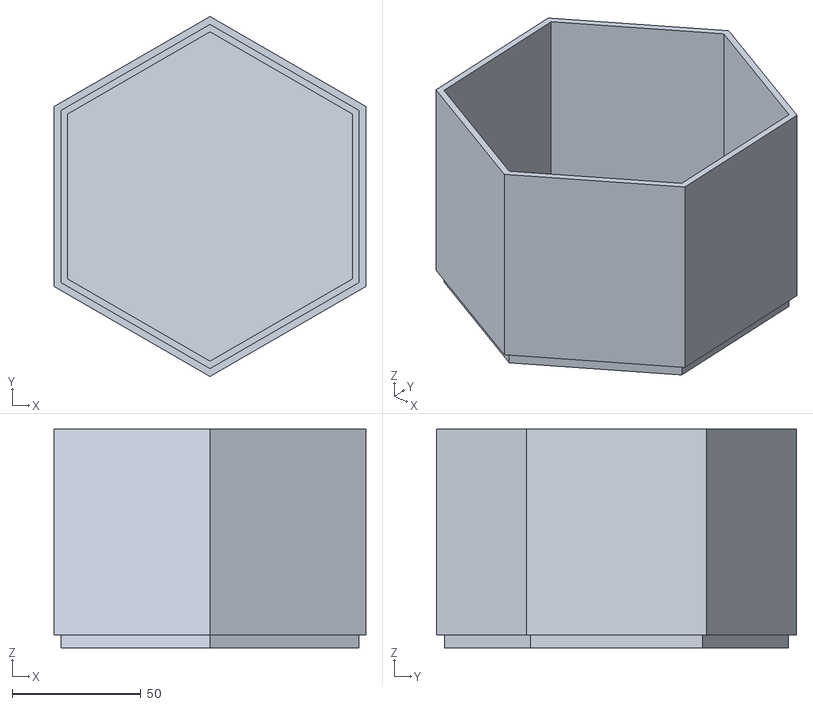
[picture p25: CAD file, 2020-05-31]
3D/stl_files/smartPot_pot2.stl
121.2 x 140.0 x 85.0

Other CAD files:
3D/blender_files/smartPot.blend
3D/blender_files/smartPot_electronics.blend
3D/blender_files/smartPot_pot1.blend
3D/blender_files/smartPot_pot2.blend
3D/blender_files/smartPot_water_container.blend

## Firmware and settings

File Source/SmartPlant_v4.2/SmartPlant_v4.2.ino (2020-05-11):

/**************************************************************
   Smart ecoPOT

   1o Γυμνάσιο Ρόδου
   	2ος Πανελλήνιος Διαγωνισμός Τεχνολογιών στην Εκπαίδευση https://robotics.ellak.gr/
   	GitHub: https://github.com/anikola57/1-GymnasioRodou

   v1, 03/12/2019:
      Αναλογικοί αισθητήρες υργασίας - Υλοποίηση βασικής λειτουργίας ποτίσματος
   v2, 09/02/2020:
      Ψηφιακοί αισθητήρες υργασίας - νερού
      Υλοποίηση με functions
   v3, 07/03/2020:
      Επικοινωνία με wifi
   v4, 21/03/2020:
      Αναλογικοί αισθητήρες υγρασίας - στάθμης νερού
      Χρόνος λειτουργίας αντλίας με χρήση της millis()
      Ρύθμιση χρόνου αναμονής
      υπολογισμός μέσης τιμής μετρήσεων
      μέτρηση τάσης μπαταρίας


  (... Στοιχεία της ομάδας ανάπτυξης....)
 **************************************************************/

#include <SoftwareSerial.h>
#include "sleep.h"

// Ορισμός δεύτερης σειριακής θύρας για αποστολή δεδομένων στο WiFi Module
SoftwareSerial mySerial(11, 12); // RX, TX


// Είσοδοι / Έξοδοι - Pins
const int redLedPin = 4;         // LED Έλλειψη νερού
const int greenLedPin = 5;       // LED Κανονική υγρασία για το φυτό
const int yellowLedPin = 3;      // LED Πότισμα
const int pumpPin = 7;           // Αντλία ποτίσματος
const int waterLevelPin = A3;      // Αισθητήρας στάθμης νερού
const int soilSensorPin = A1;  // Αισθητήρας υγρασίας χώματος
const int smSensorPowerPin = A0;     //
const int wlSensorPowerPin = A2;     //
const int wifiResetPin = 13;      // Reset για το wifi module
const int bateryVoltagePin = A5;  //Μπαταρία

// Ρυθμίσεις
int checkInterval = 900;          // Χρόνος αναμονής μεταξύ μετρήσεων 120 λεπτα (X 8 sec)
int minWaterLevel = 20;             // Ελάχιστη στάθμη νερού % στη δεξαμενή
int minMoistureLevel = 70;          // Ελάχιστη υγρασία % χώματος
int amountToPump = 20;               // Χρόνος λειτουργίας της αντλίας (sec)

// Βοηθητικές μεταβλητές
unsigned int waterLevelValue = 0;
unsigned int soilHumidityValue = 0;
float bateryVoltage = 0;
unsigned long startPumpTime;    // Χρόνος έναρξης λειτουργίας της αντλίας
bool pumping = false;        // Λειτουργία αντλίας
bool waterInTank;

/////////////////////////////////////////////////////////////////////////////////////////
/////////////////////////////////////////////////////////////////////////////////////////

// Αρχικοποίηση προγράμματος - Ρυθμίσεις που θα τρέχουν μία φορά μετά από κάθε εκκίνηση ή reset
void setup() {
  Serial.begin(9600);
  delay(10);
  mySerial.begin(38400);
  configure_wdt();

  // Ορισμός εισόδων/εξόδων
  pinMode(wifiResetPin, OUTPUT);
  pinMode(redLedPin, OUTPUT);
  pinMode(greenLedPin, OUTPUT);
  pinMode(yellowLedPin, OUTPUT);
  pinMode(pumpPin, OUTPUT);
  pinMode(smSensorPowerPin, OUTPUT);
  pinMode(wlSensorPowerPin, OUTPUT);

  // Απενεργοποίηση αισθητήρων
  digitalWrite(smSensorPowerPin, LOW);
  digitalWrite(wlSensorPowerPin, LOW);


  // Ενεργοποίηση WiFi Module
  digitalWrite(wifiResetPin, HIGH);

  Serial.println("\n\nStarting...");

  // Ένδειξη λειτουργίας του κώδικα
  blinkLeds();

  // Έλεγξε αν υπάρχει νερό στη δεξαμενή
  waterInTank = checkWaterLevel();
  Serial.print("wlsensorValue: ");
  Serial.println(waterLevelValue);

  wdt_reset();
}


// Πρόγραμμα που εκτελείται συνεχώς σε επαναλήψεις
void loop() {
  wdt_reset();

  // Ανάγνωση αισθητήρα υγρασίας
  soilHumidityValue = readSoilHumidity();
  Serial.print("soilHumidityValue: ");
  Serial.println(soilHumidityValue);

  // Μέτρηση τάσης μπαταρίας
  readBatteryValue();

  // Αν υπάρχει νερό, έλεγξε το χώμα και αν χρειάζεται πότισε
    if (waterInTank) {
      pumping = checkSoilAndWater();
    }


  // Αποστολή τιμών στον Υπολογιστή μέσω σειριακής θύρας
  sendMeasurements();

  // Αποστολή τιμών στο wifi μέσω σειριακής θύρας
  sendToWiFi();
  wdt_reset();


  // Αν ποτίζει, κλείσε την αντλία μετά από χρόνο amountToPump
  while (pumping) {
    if (checkTimeToTurnOffPump()) {
      // Έλεγξε αν υπάρχει νερό στη δεξαμενή μετά το πότισμα
      waterInTank = checkWaterLevel();      
    }
    wdt_reset();
  }

  Serial.print("sleeping...");
  delay(100);
  sleep(checkInterval);   //Κοιμήσου μέχρι την επόμενη μέτρηση
  Serial.print("wake up");
}


//####################################################################################################
//####################################################################################################

// Έλεγχος για το χρόνο ποτίσματος και σβήσιμο της αντλίας
//  Επιστρέφει TRUE όταν ολοκληρωθεί ο χρόνος ποτίσματος
bool checkTimeToTurnOffPump() {
  bool retValue = false;
  unsigned long currentMillis = millis();
  if ((unsigned long)(currentMillis - startPumpTime) > amountToPump * 1000) {
    digitalWrite(pumpPin, LOW);
    digitalWrite(yellowLedPin, LOW);
    pumping = false;
    retValue = true;
  }
  return retValue;
}


// Διαβάζει τον αισθητήρα στάθμης νερού
//  Επιστρέφει την στάθμη %
unsigned int readWlsensorValue() {
  unsigned int rawValue = 0;
  
  digitalWrite(wlSensorPowerPin, HIGH);
  delay(5);
  //  Μέσος όρος 4 μετρήσεων υγρασίας
  for (int i = 0; i < 4; i++) {
    rawValue += analogRead(waterLevelPin);
    delay(1);
  }
  digitalWrite(wlSensorPowerPin, LOW);
  rawValue /= 4;

  // Διόρθωση κλίμακας μετρήσεων
  rawValue = constrain(rawValue, 560, 665);
  rawValue = map(rawValue, 560, 665, 0, 100);
  
  return rawValue;
}


// Ανάγνωση αισθητήρα υγρασίας
//  Επιστρέφει την υγρασία %
unsigned int readSoilHumidity() {
  unsigned int rawValue = 0;

  digitalWrite(smSensorPowerPin, HIGH);
  delay(5);
  //  Μέσος όρος 4 μετρήσεων υγρασίας
  for (int i = 0; i < 4; i++) {
    rawValue += analogRead(soilSensorPin);
    delay(1);
  }
  digitalWrite(smSensorPowerPin, LOW);
  rawValue /= 4;

  // Διόρθωση κλίμακας μετρήσεων
//  rawValue = constrain(rawValue, 450, 680);
  rawValue = map(rawValue, 450, 680, 0, 100);

  return rawValue;
}


// Μέτρηση τάσης μπαραρίας
void readBatteryValue(void) {
  //  Μέσος όρος 10 μετρήσεων τάσης μπαταρίας
  bateryVoltage = 0;
  for (int i = 0; i < 10; i++) {
    bateryVoltage += analogRead(bateryVoltagePin);
    delay(10);
    wdt_reset();
  }
  bateryVoltage /= 10;
 
  // Υπολογισμός τιμής Τάσης μπαταρίας
  bateryVoltage = bateryVoltage * 5 / 1024;
}



// Αποστολή τιμών στον Υπολογιστή μέσω σειριακής θύρας
void sendMeasurements() {
  Serial.print("WaterLevel: ");
  Serial.println(waterLevelValue);
  Serial.print("Moisture: ");
  Serial.println(soilHumidityValue);
  Serial.print("Voltage: ");
  Serial.println(bateryVoltage);
}

// Αποστολή μετρήσεων στο WiFi module
void sendToWiFi() {
  // Wake up wifi module
  digitalWrite(wifiResetPin, LOW);
  delay(10);
  digitalWrite(wifiResetPin, HIGH);
  delay(2000);
  mySerial.print(waterLevelValue);
  mySerial.print(",");
  mySerial.print(soilHumidityValue);
  mySerial.print(",");
  if (digitalRead(pumpPin)) {
    mySerial.print("1");
  } else {
    mySerial.print("0");
  }
  mySerial.print(",");
  mySerial.print(bateryVoltage);

  mySerial.print(",");
  mySerial.print("0");
  mySerial.print(",");
  mySerial.print("0");

  mySerial.print("\n");

}


// Έλεγξε αν υπάρχει νερό στη δεξαμενή
bool checkWaterLevel() {
  waterLevelValue = readWlsensorValue();
  if (waterLevelValue > minWaterLevel) {
    digitalWrite(redLedPin, LOW);
    return true;
  }
  digitalWrite(redLedPin, HIGH);
  return false;
}


// Έλεγχος υγρασίας και ποτίσματος
// Επιστρέφει true ή false ανάλογα αν λειτουργει η αντλια
bool checkSoilAndWater() {
  // Αν υπάρχει ξηρασία στο χώμα, πότισε και τροποποίησε τις ενδείξεις
  if (soilHumidityValue < minMoistureLevel) {
    digitalWrite(greenLedPin, LOW);
    digitalWrite(yellowLedPin, HIGH);   // Ένδειξη ποτίσματος
    digitalWrite(pumpPin, HIGH);      // Λειτουργία αντλίας
    startPumpTime = millis();       //Χρόνος έναρξης αντλίας
    return true;
  }
  // Αλλιώς τροποποίησε τις ενδείξεις
  else {
    digitalWrite(greenLedPin, HIGH);  // Ικανοποιητική υγρασία
    digitalWrite(yellowLedPin, LOW);
  }
  return false;
}


void blinkLeds() {
  for (int i = 0; i < 2; i++) {
    digitalWrite(redLedPin, HIGH);
    delay(100);
    digitalWrite(redLedPin, LOW);
    digitalWrite(yellowLedPin, HIGH);
    delay(100);
    digitalWrite(yellowLedPin, LOW);
    digitalWrite(greenLedPin, HIGH);
    delay(100);
    digitalWrite(greenLedPin, LOW);
  }
}
//--------------------------------------------------------------------------------------

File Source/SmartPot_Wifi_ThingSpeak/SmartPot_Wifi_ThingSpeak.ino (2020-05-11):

/*
     Smart ecoPOT

   1o Γυμνάσιο Ρόδου
     2ος Πανελλήνιος Διαγωνισμός Τεχνολογιών στην Εκπαίδευση https://robotics.ellak.gr/
    GitHub: https://github.com/anikola57/1-GymnasioRodou

  
  Λήψη δεδομένων από Arduino και ενημέρωση ThingSpeak
  https://thingspeak.com/channels/1026147
*/

#include "ThingSpeak.h"
#include "secrets.h"
#include <ESP8266WiFi.h>
//#include <Wire.h>


char ssid[] = SECRET_SSID;   // your network SSID (name) 
char pass[] = SECRET_PASS;   // your network password
int keyIndex = 0;            // your network key Index number (needed only for WEP)
WiFiClient  client;

unsigned long myChannelNumber = SECRET_CH_ID;
const char * myWriteAPIKey = SECRET_WRITE_APIKEY;

// Μεταβλητές δεδομένων
String receivedData = "";
String pumpStatus = "";
String battery = "";
String soilHumidity = "";
String waterLevel = "";
String data1 = "";
String data2 = "";
boolean dataComplete;


//================================================
//            Setup
//================================================
void setup() {
  dataComplete = false;
  Serial.begin(38400);  // Initialize serial
  // Wait for serial to initialize.
  while(!Serial) { }
  Serial.println("\nStarting...");
  
  WiFi.mode(WIFI_STA); 
  ThingSpeak.begin(client);  // Initialize ThingSpeak

  // Αναμονή για λήψη δεδομένων στη σειριακή
  while (!dataComplete) {
    if (Serial.available()) {
       readData();
    }
  }

  // Όταν ληφθούν νέα δεδομένα, ενημέρωσε τις μεταβλητές
  updateData();
  //Σύνδεση στο wifi
  connectWifi();
  //Αποστολή δεδομένων στο Thing Speak
  updateThingSpeak();
  Serial.println("Going to sleep!");
  ESP.deepSleep(0); 
}

void loop() {
}


//===============================================================
// Ρουτίνες επικοινωνίας
//===============================================================

void connectWifi() {
  // Connect or reconnect to WiFi
  if(WiFi.status() != WL_CONNECTED){
    Serial.print("Attempting to connect to SSID: ");
    Serial.println(SECRET_SSID);
    while(WiFi.status() != WL_CONNECTED){
      WiFi.begin(ssid, pass);  // Connect to WPA/WPA2 network. Change this line if using open or WEP network
      Serial.print(".");
      delay(5000);     
    } 
    Serial.println("\nConnected.");
  }
}

// Ενημερώνει τα δεδομένα στο κανάλι του Thing speak
void updateThingSpeak() {
  // set the fields with the values
  ThingSpeak.setField(1, soilHumidity.toInt());
  ThingSpeak.setField(2, waterLevel.toInt());
  ThingSpeak.setField(3, pumpStatus.toInt());
  ThingSpeak.setField(4, battery.toFloat());

  ThingSpeak.setField(5, data1.toFloat());
  ThingSpeak.setField(6, data2.toFloat());
    
  // set the status
//  ThingSpeak.setStatus(pumpStatus);
  
  // write to the ThingSpeak channel
  int x = ThingSpeak.writeFields(SECRET_CH_ID, SECRET_WRITE_APIKEY);    //changes only here***
  if(x == 200){
    Serial.println("Channel update successful.");
  }
  else{
    Serial.println("Problem updating channel. HTTP error code " + String(x));
  }
}

//===============================================================
// Ρουτίνες ανάγνωσης και ενημέρωσης δεδομένων
//===============================================================

// Ενημέρωση μεταβλητών με τα νέα δεδομένα από τη σειριακή επικοινωνία
void updateData() {
  int firstComma = receivedData.indexOf(',');
  waterLevel = receivedData.substring(0, firstComma); // Στάθμη νερού
  int secondComma = receivedData.indexOf(',', firstComma + 1);
  soilHumidity = receivedData.substring(firstComma + 1, secondComma); // 
  int thirdComma = receivedData.indexOf(',', secondComma + 1);
  pumpStatus = receivedData.substring(secondComma + 1, thirdComma); // 

  int nextComma = receivedData.indexOf(',', thirdComma + 1);
  battery = receivedData.substring(thirdComma + 1, nextComma); // 
  secondComma = receivedData.indexOf(',', nextComma + 1);
  data1 = receivedData.substring(nextComma + 1, secondComma); // 
  thirdComma = receivedData.lastIndexOf(',');
  data2 = receivedData.substring(thirdComma + 1, receivedData.length());

  // Εκκαθάριση μεταβλητής για την επόμενη λήψη δεδομένων
  receivedData = "";
}

// Ανάγνωση δεδομένων από τη σειριακή θύρα επικοινωνίας
void readData() {
  while (Serial.available()) {
    // get the new byte:
    char inChar = (char)Serial.read();    
    if (!dataComplete) {
      // add it to the inputString:
      if (inChar != '\n') {
        receivedData += inChar;
      }
      // if the incoming character is a newline, set a flag
      // so the main loop can do something about it:
      if (inChar == '\n') {
        dataComplete = true;
      }
    }
    // Έλεγχος για τυχόν λειτουργίες WiFi
    yield();
  }
}

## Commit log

2019-11-25 ...in progress..
    [SmartPlant_basic_v1.fzz]
2020-05-11 New schematics and source v4
    [SmartPlant_basic_v1.fzz, SmartPlant_schematics.fzz]
2020-05-18 Βίντεο
